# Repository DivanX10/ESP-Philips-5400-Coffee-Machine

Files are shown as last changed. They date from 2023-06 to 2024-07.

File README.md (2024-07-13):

### [Read in English here](https://github.com/DivanX10/ESP-Philips-5400-Coffee-Machine/blob/main/README_EN.md)

# ESP-Philips-5400-Coffee-Machine

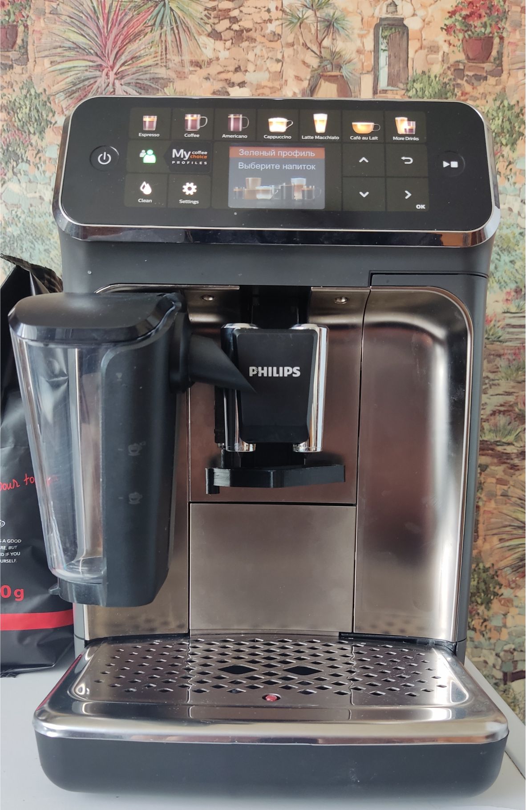
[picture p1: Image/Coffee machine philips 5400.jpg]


***

### Выражаю благодарность участникам чата [ESPHome](https://t.me/esphome) и [Умный дом с диваном](https://t.me/smart_home_divan), а также огромное спасибо [Brokly](https://github.com/Brokly) за неоценимый вклад в данный проект, который написал код для управления кофемашиной. 

***

Важно! Собирать прошивку строго в ESPHome версии 2023.5.0 или 2023.6.0 и не позднее, а также в конфигурации указывать конкретную версию arduino 2.0.9. Если соберете прошивку в последней версии ESPHome и будете использовать arduino recommended, то кофемашина будет сбоить, будет работать некорректно. Нужно переписывать код. Если имеете желание переписать код под новую версию ESPHome и поделитесь, то буду вам благодарен за участие. Спасибо. 

```
esp32:
  board: esp32dev
  framework:
    type: arduino
    version: 2.0.9
```
<details>
  <summary>Как установить любую версию аддона ESPHome?</summary>

1) Скачать нужную версию аддона ESPHome можно по этой [ссылке](https://github.com/esphome/home-assistant-addon)
 * Скачать аддон ESPHome 2023.5.0 (17.05.2023) [здесь](https://github.com/esphome/home-assistant-addon/releases/tag/2023.5.0)
 * Скачать аддон ESPHome 2023.6.0 (22.06.2023) [здесь](https://github.com/esphome/home-assistant-addon/releases/tag/2023.6.0)
2) Распаковать архив в любое место чтобы можно было скопировать в Home Assistant
3) Копируем папку **esphome** из архива в сетевую папку **addons**. Если сетевые папки Home Assistant не работают, то установить аддон **Samba share**. Аддон **Samba share** по умолчанию доступен в магазине аддонов, но если аддона **Samba share** по каким-то причинам нет, то включите расширенный режим и тогда в магазине аддонов вы увидите аддон **Samba share**, а если этого аддона по прежнему нет, то можете установить аддон **Samba share** по этой [ссылке](https://github.com/home-assistant/addons/tree/master/samba)

 * Как включить Расширенный режим?   


 * Куда скачать файл **esphome**?

В архиве **home-assistant-addon-xx.xx.xxxx** нас интересует папка **esphome**


Папку **esphome** копируем в сетевую папку **addons**



4) Перезагружаем Home Assistant
5) Заходим в магазин аддонов и ищем локальную версию аддона ESPHome. Смотрим на версию, должна быть версия 2023.5.0 или 2023.6.0, в зависимости какой архив мы скачали


8) Если локальная версия аддона ESPHome есть и версия 2023.5.0 или 2023.6.0, то ставим

</details>

***

Модификация и удаленное управление кофемашиной Philips 5400. Управление реализовано средствами UART и ESPHome.

> Важно!
Все материалы этого проекта (прошивки, схемы, 3D модели и т.п.) предоставляются "КАК ЕСТЬ". Всё, что вы делаете с вашим оборудованием, вы делаете на свой страх и риск. Автор не несет ответственности за результат и ничего не гарантирует. Модификация кофемашины требует вмешательства, что лишит автоматически вас гарантии на новую кофемашину.

> Рабочие варианты кода для управления кофемашиной можно взять [**здесь**](https://github.com/DivanX10/ESP-Philips-5400-Coffee-Machine/tree/main/Config/ESPHome) (читайте комментарии в коде)

***

<details>
  <summary>Что умеет делать интеграция?</summary>

1) Включать и выключать кофемашину
2) Выбрать кофейный напиток
   * Эспрессо
   * Эспрессо лунго
   * Кофе
   * Американо
   * Капучино
   * Латте макиато
   * Кофе с молоком
   * Кофе латте
   * Кафе крема
   * Ристретто
   * Кофе в дорогу
   * Кофе с молоком в дорогу
   * Молочная пена
   * Горячая вода
3) Выбрать крепость кофе
4) Выбрать зерно или молотый
5) Выбрать количество порции, в том числе и ExtraShot
6) Выбрать объем кофе
7) Выбрать объем молока
8) Отправлять собственные рецепты кофейных напитков
9) Автоматическая работа отвода воды от носика кофемашины
10) Калибровка сервопривода для отвода воды
11) Сенсоры
    * Поддон
    * Зерно
    * Вода в контейнере
    * Контейнер кофейной гущи
    * Поддон и контейнер воды извлечены
    * Статус питания кофемашины (включена/выключена)
    * Статусы кофемашины (приготовление, наливаем кофе, наливаем молоко, перемалываем зерна и т.д)
    * Сенсор ошибки
    * Сенсор 90 для отображения пакета рецепта кофейных напитков, этот пакет можете использовать для создания своего любимого рецепта кофейного напитка
    * Сенсор выбранного кофейного напитка, обема кофе и молока

</details>

<details>
  <summary>Добавление компонета Philips 5400 в ESPHome</summary>
  
```
external_components:
  - source:
      type: git
      url: https://github.com/DivanX10/ESP-Philips-5400-Coffee-Machine

```

При желании можно подключить компонент локально. Скачайте файлы в папку \esphome\components\ 

```
external_components:
  - source:
      type: local
      path: components
    components: [philips_series_5400]

```

</details>

<details>
  <summary>Примеры отправки собственных кофейных напитков</summary>

> Это чисто рекомендация и уведомление. Решение принимать вам. У данной модели любые изменения параметра напитка сохраняются в профиль, кроме гостевого профиля. Чтобы не перезаписывать профили, можете выбрать гостевой профиль и посылая рецепты на приготовление, изменения не будут перезаписаны. Когда отправляете любой напиток, на экране не будет отображаться выбранный вами напиток, а будет отображаться тот напиток, который вы выбирали последний раз на панели управления кофемашины. Если не трогали экран, то по умолчанию будет выбираться первый напиток, это эспрессо   

Если включить сенсор Messge2 90, то в нем будет отображаться пакет кофейного напитка. Вы можете это использовать для своих рецептов. Просто скопируйте все байты, кроме первых трех (пример на скриншоте, выделено красным)



Вы можете создавать любые рецепты используя таблицу [**протокола кофейных напитков**](https://github.com/DivanX10/ESP-Philips-5400-Coffee-Machine/raw/main/Protocol/Протокол%20кофейных%20напитков%20и%20программы.xlsx) в Excel

```
button:

#Пример кода для отправки кофейного напитка Кофе Max 150ml. Пакет рецепта копируется с сенсора Messge2 90, отсеиваем только первые 3 байта
#Напиток: Кофе. Зерно: Максимум. Кофе: 150 мл.
  - platform: template
    name: "Кофе Max 150ml"
    icon: mdi:coffee
    on_press:
      - lambda: |-
          {
            uint8_t data[]={0x00, 0x03, 0x00, 0x02, 0x02, 0x00, 0x96, 0x00, 0x00, 0x00};
            id(philip)->prepare(data);
          }

#Пример кода для отправки кофейного напитка Американо молотый 90ml. Пакет рецепта копируется с сенсора Messge2 90, отсеиваем только первые 3 байта
  - platform: template
    name: "Американо молотый 80ml"
    icon: mdi:coffee
    on_press:
      - lambda: |-
          {
            uint8_t data[]={0x01, 0x00, 0x00, 0x02, 0x03, 0x00, 0x28, 0x00, 0x28, 0x00};
            id(philip)->prepare(data);
          }

#Пример кода для отправки кофейного напитка Кофе с молоком 150/120ml. Пакет рецепта копируется с сенсора Messge2 90, отсеиваем только первые 3 байта
  - platform: template
    name: "Кофе с молоком Max 150/120ml"
    icon: mdi:coffee
    on_press:
      - lambda: |-
          {
            uint8_t data[]={0x02, 0x03, 0x00, 0x02, 0x01, 0x02, 0x96, 0x00, 0x78, 0x00};
            id(philip)->prepare(data);
          }

```
</details>

<details>
  <summary>Встраиваем ESP</summary>

Снимаем панель управления. Снимается не сложно. Чуть тянем на себя, в эти точки вставляем пластиковую лопатку и вынимаем панель



Нам нужен доступ к 8-ми жильному проводу, который нужно подключить к ESP. 





> Подключаем по схеме на выбор, через реле или через оптопару. Сервопривод подключаем по желанию, он нужен для работы отвода воды от носика.

### Общая схема подключения без реле и оптопары. Просто подключение ESP32 к кофемашине



***

### Схема с подключением реле 5В (KY-019)



***

### Cхема с подключением оптопары PC817C



</details>

<details>
  <summary>Разбираем панель управления</summary>

Почему именно я разобрал панель управления и подключил реле, и почему не оптопару? Были попытки найти решение включить кофемашину без разборки панели управления. Пробовал размыкать питание через транзистор, пробовал посылать посылать команды, но это было безуспешно. 

Подключал резистор по такой схеме, но этот способ работает на кофемашине серии 2000/3000, но не подошел для серии 5400. Для справки, есть два проекта для кофемашин серии 2000, это [ESPHome-Philips-Smart-Coffee]( https://github.com/TillFleisch/ESPHome-Philips-Smart-Coffee) и [SmartPhilips2200](https://github.com/chris7topher/SmartPhilips2200)

Снимаем наклейку с чипа и видим маркировку с названием чипа STM32L4R5VIT6




В документации чипа [STMicroelectronics STM32L4R5VIT6](https://github.com/DivanX10/ESP-Philips-5400-Coffee-Machine/blob/main/Documentation/STMicroelectronics%20STM32L4R5VIT6.pdf) находим наш чип, это STM32L4R5VIT6 LQFP100 (25 ножек с каждой стороны)



В документации пишется, что управлять кофемашиной байтами можно после включения, поэтому у меня и не получилось включить ее удаленно. Возможно я ошибаюсь и если будет найдено такое решение, то обязательно внесу поправку



***

Для имитации работы сенсорной кнопки можно использовать модуль реле одноканальный 5В (KY-019) или оптопару PC817C, которые будут подавать GND на резистор R110, к которому идет дорожка от кнопки питания, тем самым включая и выключая кофемашину. Я не стал рисковать припаивать провод после резистора R110 (номинал резистора 4,7 кОм), так как после резистора идет прямая дорожка к ножке чипа, а лампе к конденсаторам и я не знаю как чип может на это отреагировать, но, если так сделать, то тогда у нас будет возможность включать кофемашину через сенсорную кнопку и удаленно. Это было проверенно на сенсорной лампе, где я припаял провода после резистора и я мог включать и выключать удаленно, а также включать и выключать лампу нажимая на сенсорную кнопку. На кофемашине я не решаюсь это повторить.

Панель управления в разборе




Дорожка от кнопки питания к резистору R110(номинал резистора 4,7 кОм), после резистора дорожка идет к [диоду шоттки BAS70TW (K73)](https://github.com/DivanX10/ESP-Philips-5400-Coffee-Machine/blob/main/Documentation/Диод%20шоттки%20BAS70TW%20(K73).pdf)





Припаиваем провод к резистору R110(номинал резистора 4,7 кОм)



Делаем отверстие в крышке и выносим провод наружу, который подключим к реле или к оптопаре



</details>

<details>
  <summary>Расшифровка протокола</summary>

> Мне удалось расшифровать часть протоколов, если вы найдете что-то новое, сообщите мне об этом обновлю информацию. Создайте ишью и опишите подробно про протокол. 

Краткое описание функции протоколов

* **AA:AA:AA:90** - рецепты кофейных напитков
* **AA:AA:AA:91** - счетчик приготовления кофейных напитков
* **AA:AA:AA:93** - счетчик приготовления кофейных напитков
* **AA:AA:AA:B0** - системные сенсоры
* **AA:AA:AA:B5** - счетчик объема кофе и молока для приготовления кофейных напитков
* **AA:AA:AA:BA** - не смог расшифровать
* **AA:AA:AA:BB** - не смог расшифровать
* **AA:AA:AA:FF** - данные с ЖК экрана
* **AA:AA:AA:FE** - включение и выключение кофемашины

***

**AA:AA:AA:FE** - этот пакет AA:AA:AA:FE:00:00:C8:87:1B:40:55 встречается два раза, в самом начале, он идет первым, когда включаем кофемашину и при выключении

**AA:AA:AA:90** - протокол кофейных напитков




**AA:AA:AA:91** - протокол счетчика кофейных напитков. Это просто учет сделанных кофейных напитков и учет сбрасывается, когда кофемашина выключается. Сделали одну чашку кофе, сработал счетчик и выставил допустим 1, потом сделали еще чашку кофе, снова сработал счетчик и выставил 2. Чтобы удаленно запускать приготовление кофейных напимтков, нужно запускать на +1 к тому, что в счетчике. Без учета этого счетчика не будет срабатывать приготовление кофейных напитков удаленно



**AA:AA:AA:B0** - протокол системных сенсоров: контейнер кофейной гущи, воды, поддона, анличие зерна, статусы приготовления кофе, статусы заварного блока



**AA:AA:AA:B5** - протокол счетчика кофейных напитков. Считает в секундах объем налитого кофе и молока



</details>

<details>
  <summary>Отвод воды носика кофемашины</summary>

Я разработал для кофемашины отвод воды от носика. Зачем это нужно? Когда включаем кофемашину, то при включении запускается прогрев и промывка. Во время промывки большая часть воды проходит внутри, а часть выливается через носик. Что делать, если мы хотим, чтобы утром кофемашина приготовила нам свежее кофе и чтобы в кофе не было воды после промывки? Отвод воды позволяет решить эту проблему. Когда кофемашина включается с помощью умного дома, то отовод воды все еще остается у носика вполть до того момента, когда кофемашина не передейдет в режим "Выбор напитка", только после этого отвод воды прячется во внутрь носика, открывая проход носику.

Готовую модель для распечатки на 3д принтере можете [здесь](https://www.thingiverse.com/thing:6073849) или [скачать с этого проекта](https://github.com/DivanX10/ESP-Philips-5400-Coffee-Machine/tree/main/3D%20Model). Файлы формата FCStd можете открыть в программе FreeCAD. 

Используется сервопривод MG90S Micro Servo 180 градусов. Его вполне достаточно для отвода воды. Питаем от +3,3в от самого ESP, что является большим плюсом. Провод от сервопривода во внутрь протягивается просто, без сверления корпуса. Протискиваем провод во внутрь держателя носика и тянем к внутренней части корпуса к ESP




</details>

<details>
  <summary>Панель управления в Home Assistant</summary>





Скопируйте код [отсюда](https://github.com/DivanX10/ESP-Philips-5400-Coffee-Machine/blob/main/Config/Home%20Assistant/coffee_machine_philips_5400_ru.yaml), а после создайте карточку

Код карточки
```
entity: sensor.coffee_machine_power_status
type: custom:multiple-entity-row
name: Статус
icon: mdi:coffee-maker
state_color: true
show_state: false
secondary_info:
  attribute: Making coffee
entities:
  - entity: group.kitchen_coffee_machine_info_and_menu
    name: Меню
    state_color: true
    icon: mdi:information-outline
    styles:
      height: 60px
      width: 50px
  - entity: group.kitchen_coffee_machine_coffee_drinks
    name: Напитки
    state_color: true
    icon: mdi:coffee
    styles:
      height: 60px
      width: 50px
  - entity: switch.coffee_philips_5400_valve_open_closed
    name: Клапан
    type: switch
    tap_action:
      action: toggle
    icon: mdi:coffee-maker-outline
    state_color: true
    styles:
      height: 60px
      width: 50px
  - entity: binary_sensor.coffee_philips_5400_power_status
    name: Питание
    icon: mdi:gesture-tap-button
    state_color: true
    tap_action:
      action: call-service
      service: script.kitchen_coffee_machine_power
    styles:
      height: 60px
      width: 50px

```
</details>

</details>

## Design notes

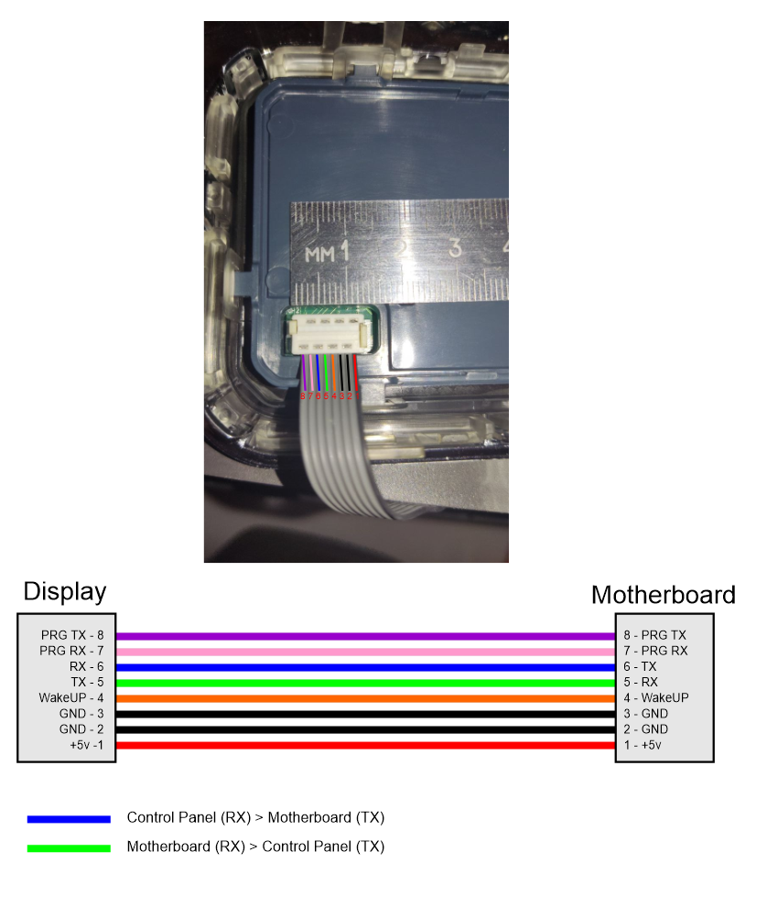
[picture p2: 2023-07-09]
Image/Pinout of 8-core wire en.png

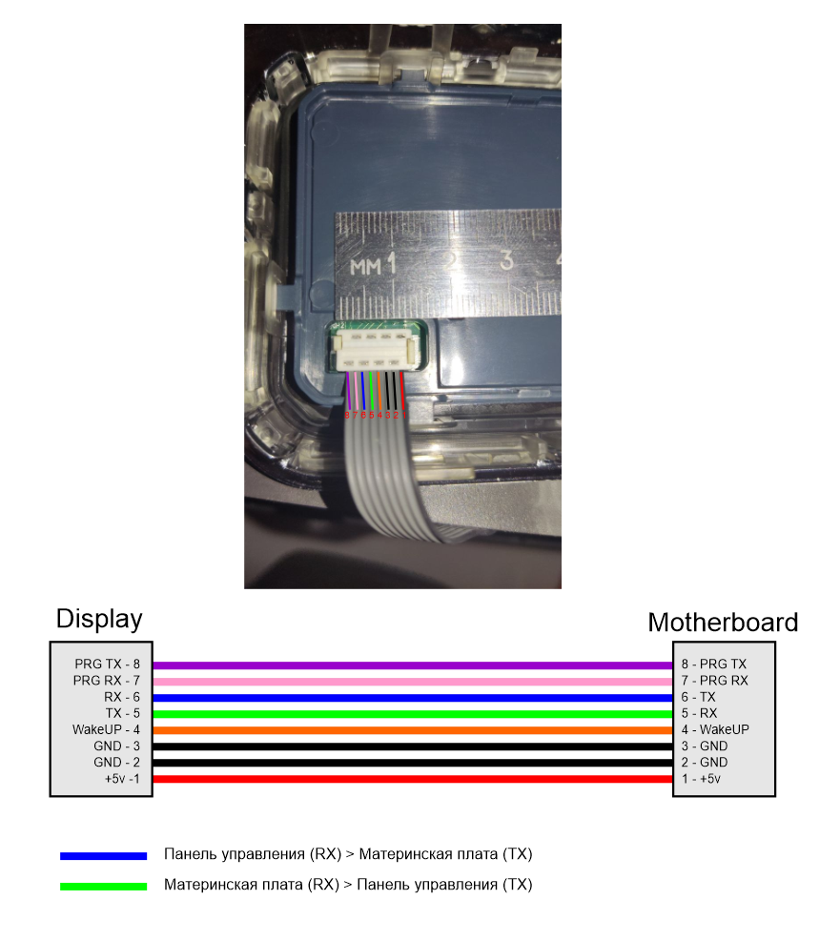
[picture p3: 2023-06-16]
Image/Pinout of 8-core wire.png

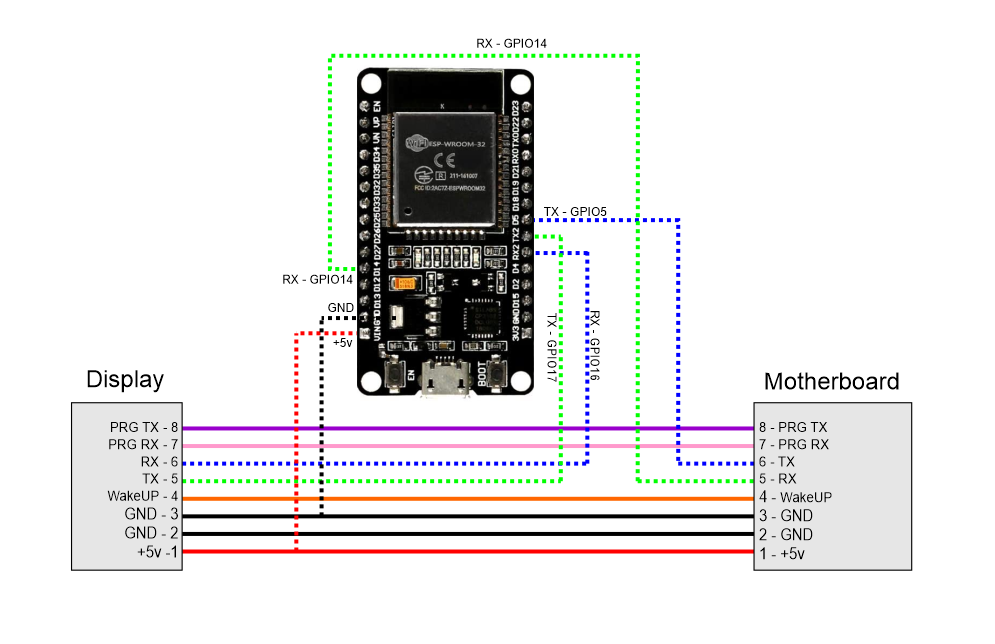
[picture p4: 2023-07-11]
Image/ESP connection diagram.png

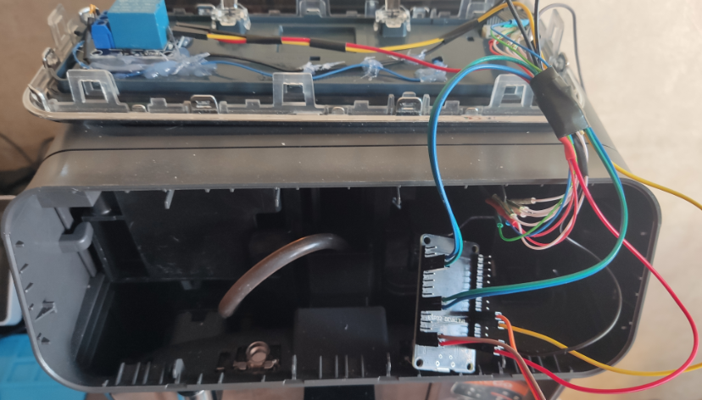
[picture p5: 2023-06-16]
Image/Connecting ESP.png

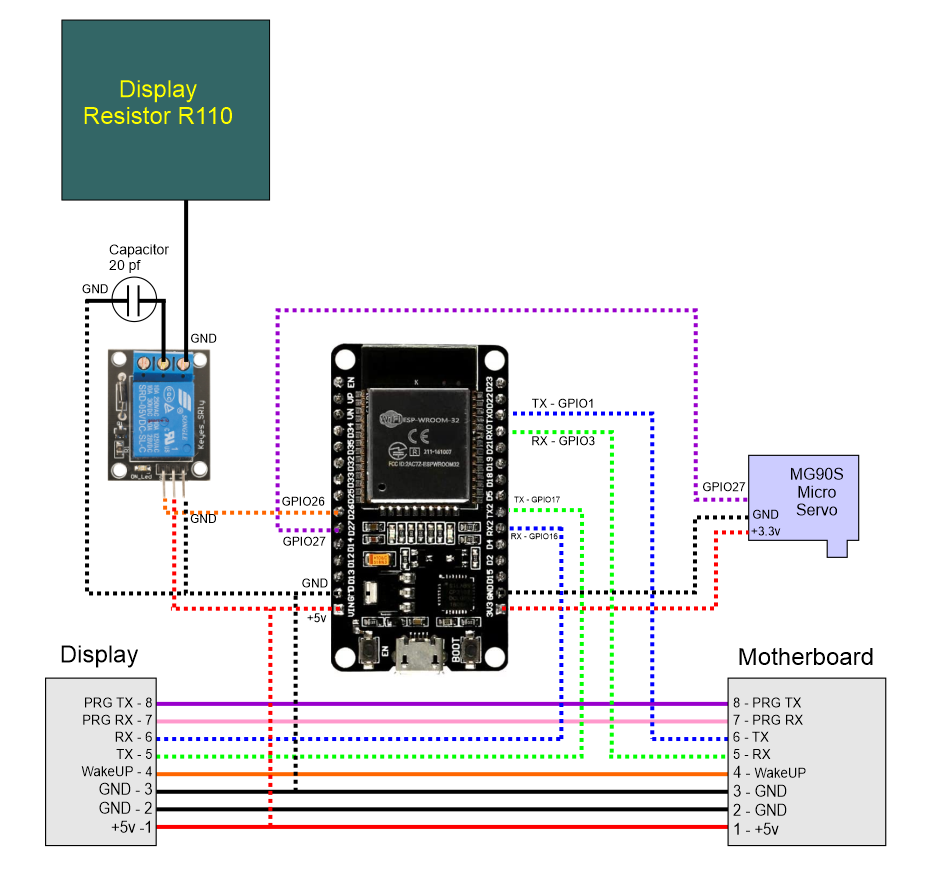
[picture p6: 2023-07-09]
Image/ESP + KY-019 relay + servo connection diagram.png

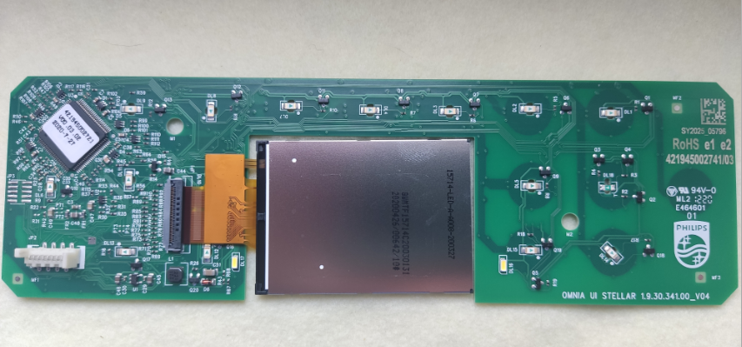
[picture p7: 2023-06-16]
Image/Chamber from the control panel.png

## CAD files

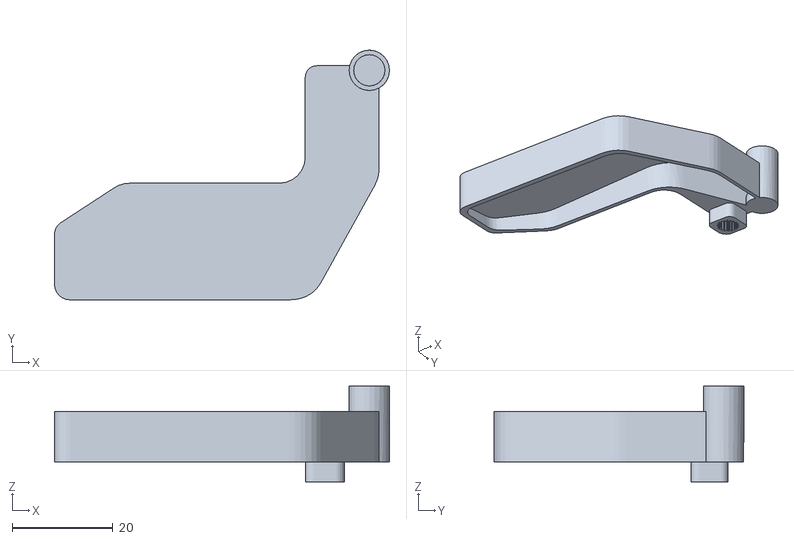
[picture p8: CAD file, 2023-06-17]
3D Model/Drainage of water from the spout.stl
66.4 x 49.5 x 19.0

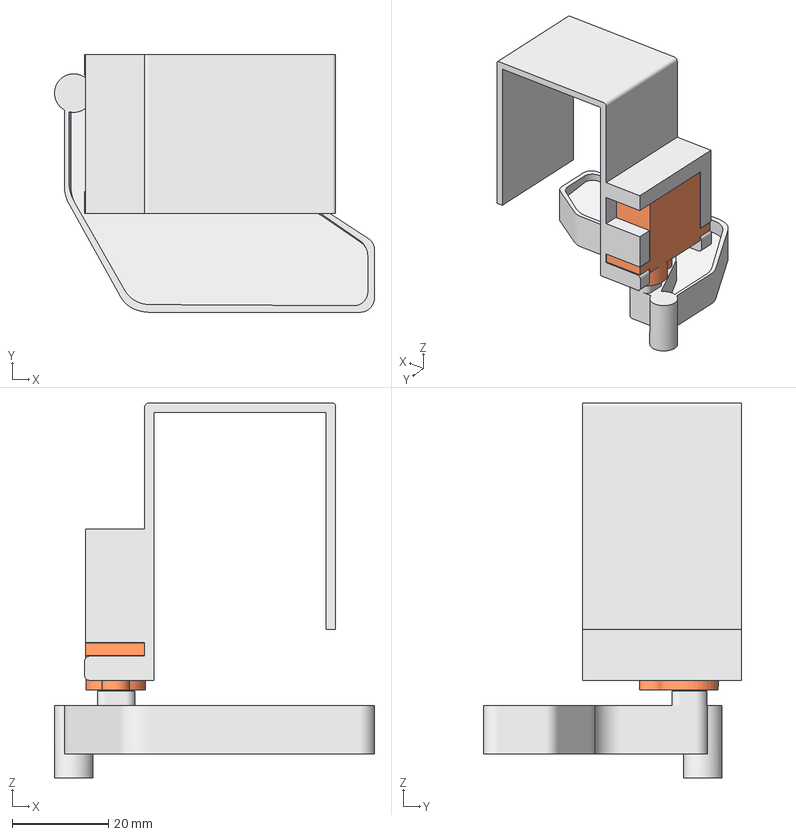
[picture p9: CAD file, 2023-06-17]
3D Model/Serva holder on the spout bracket.FCStd
66.4 x 53.5 x 77.8 mm
Держатель сервы002
Отвод воды с носика (Вариант 2)
MG90S Micro Servo

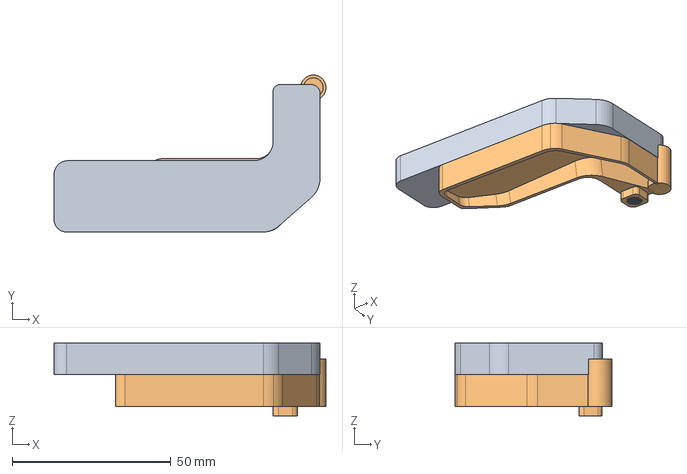
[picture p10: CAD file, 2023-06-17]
3D Model/Water drain of the coffee machine spout.FCStd
85.7 x 49.5 x 23.0 mm
Отвод воды с носика006

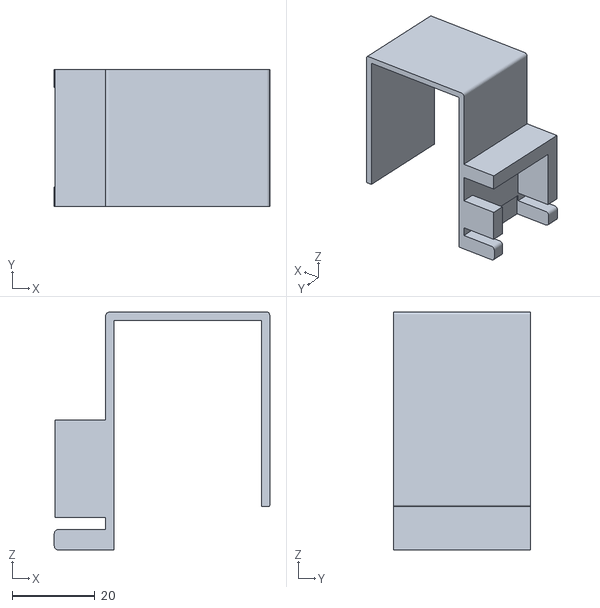
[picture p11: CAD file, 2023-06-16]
3D Model/Serva holder.stl
52.1 x 33.0 x 57.5

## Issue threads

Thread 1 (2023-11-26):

Power up without cleaning cycle

Sandst4, 2023-11-26:
First of all, amazing what you have accomplished! Really nice to be able to connect the 5400 to home assistant.

I've came across this project through here:

https://github.com/TillFleisch/ESPHome-Philips-Smart-Coffee

Inside that project they have been able to turn on the Philips Series 2200 without it starting the cleaning cycle. They accomplish this by sending a specific command. Do you think this could be possible for the 5400 as well?

I love your 3D printed solution, however, being able to skip the cleaning cycle and only do it when turning off would be amazing. Thanks!

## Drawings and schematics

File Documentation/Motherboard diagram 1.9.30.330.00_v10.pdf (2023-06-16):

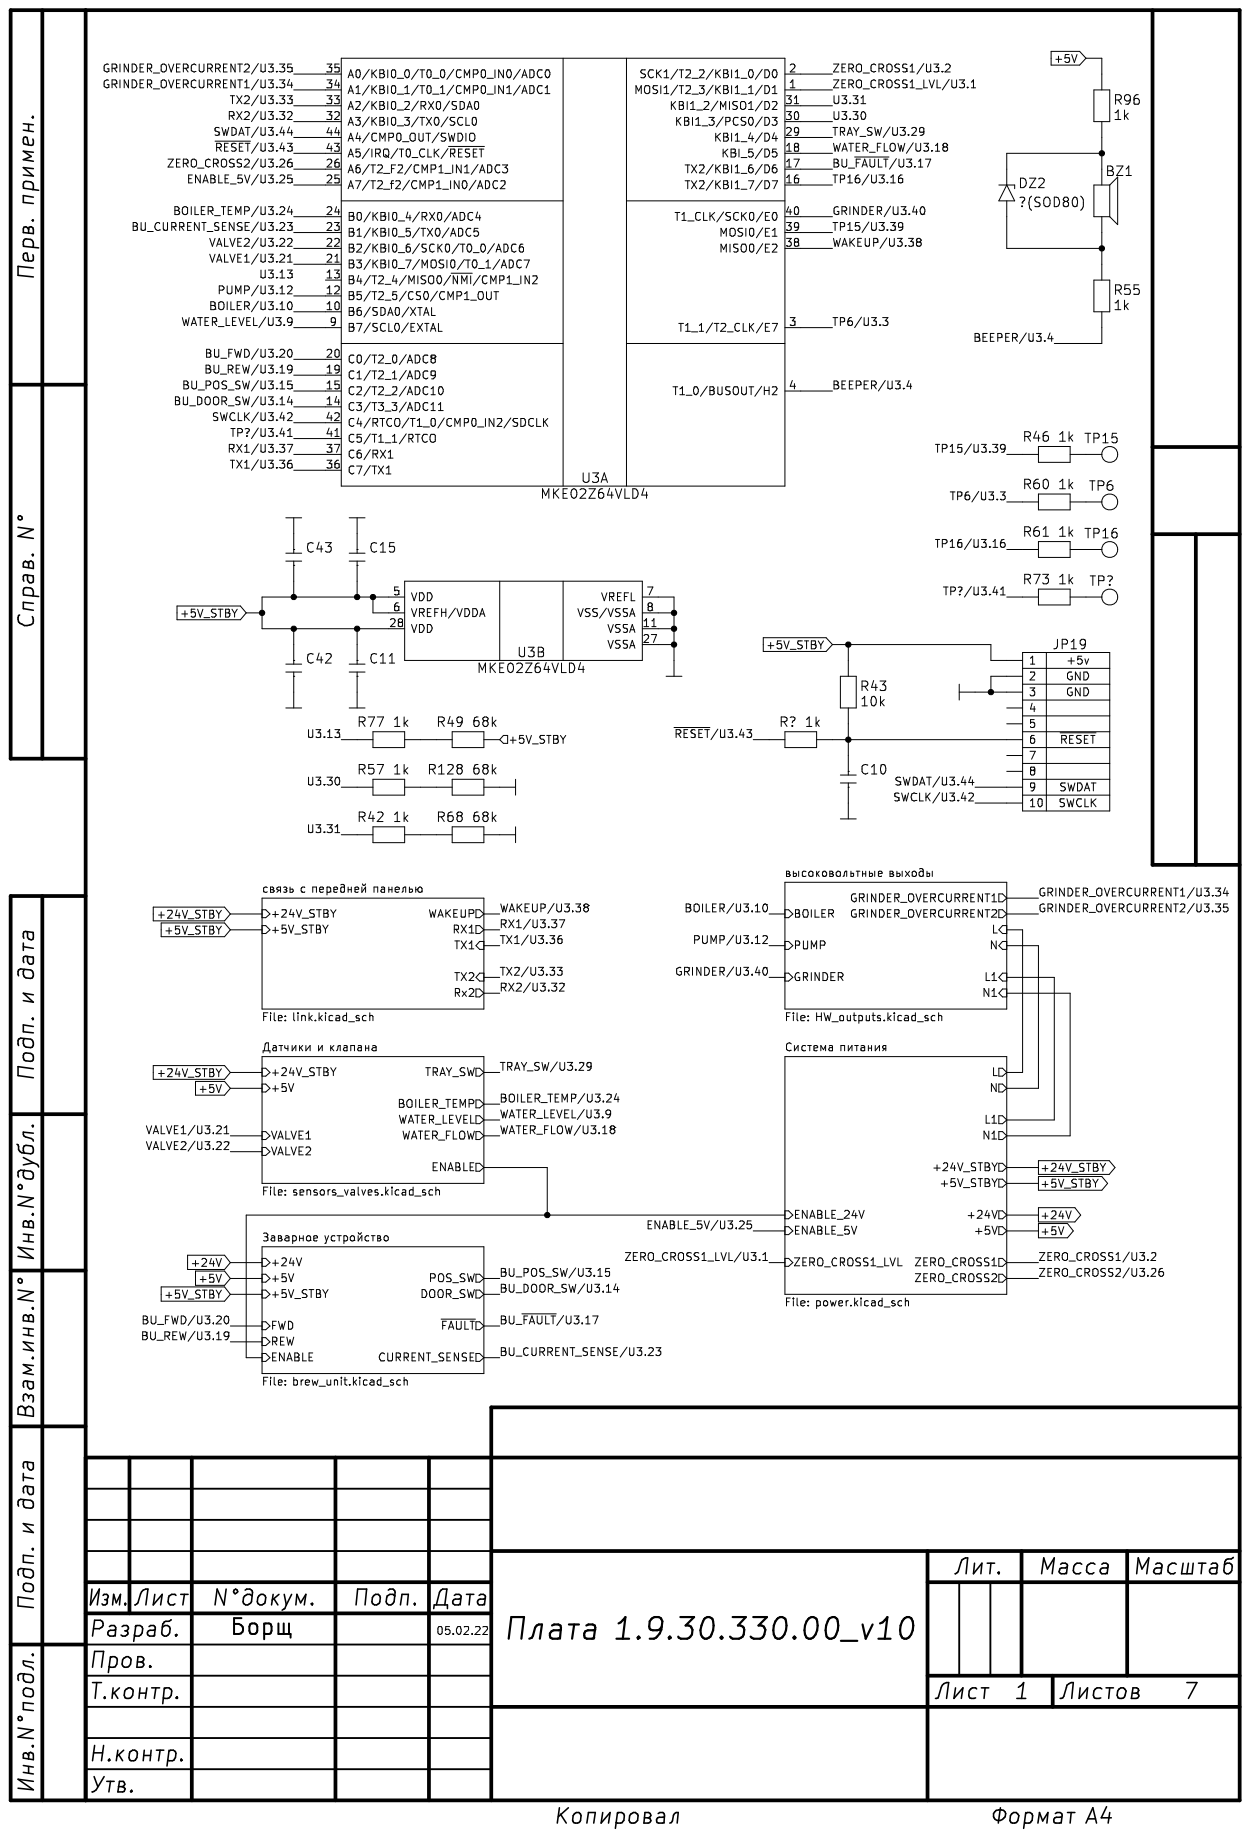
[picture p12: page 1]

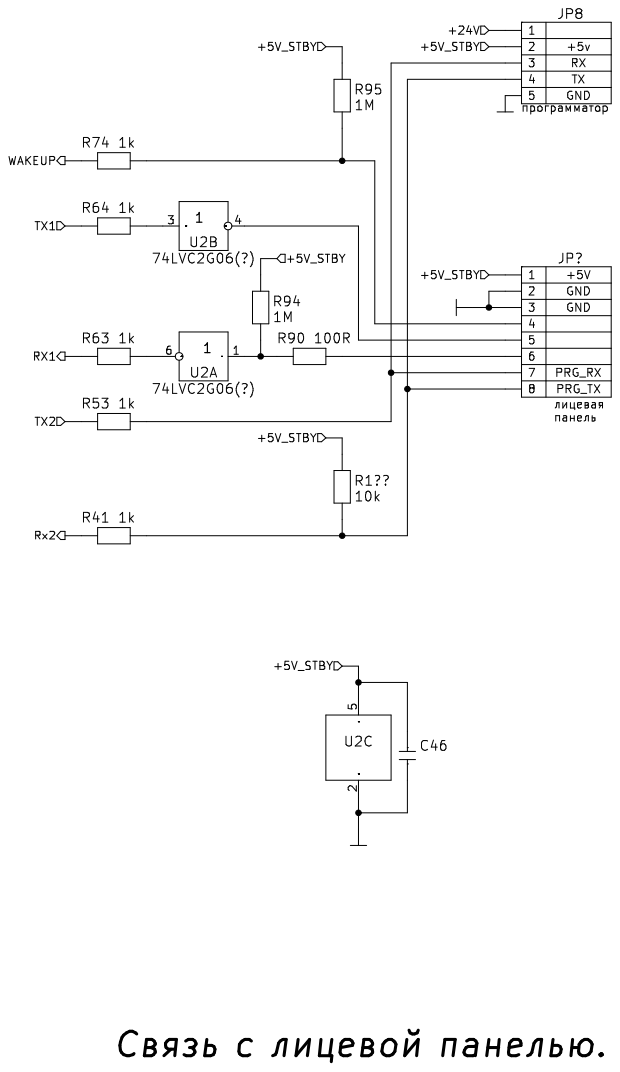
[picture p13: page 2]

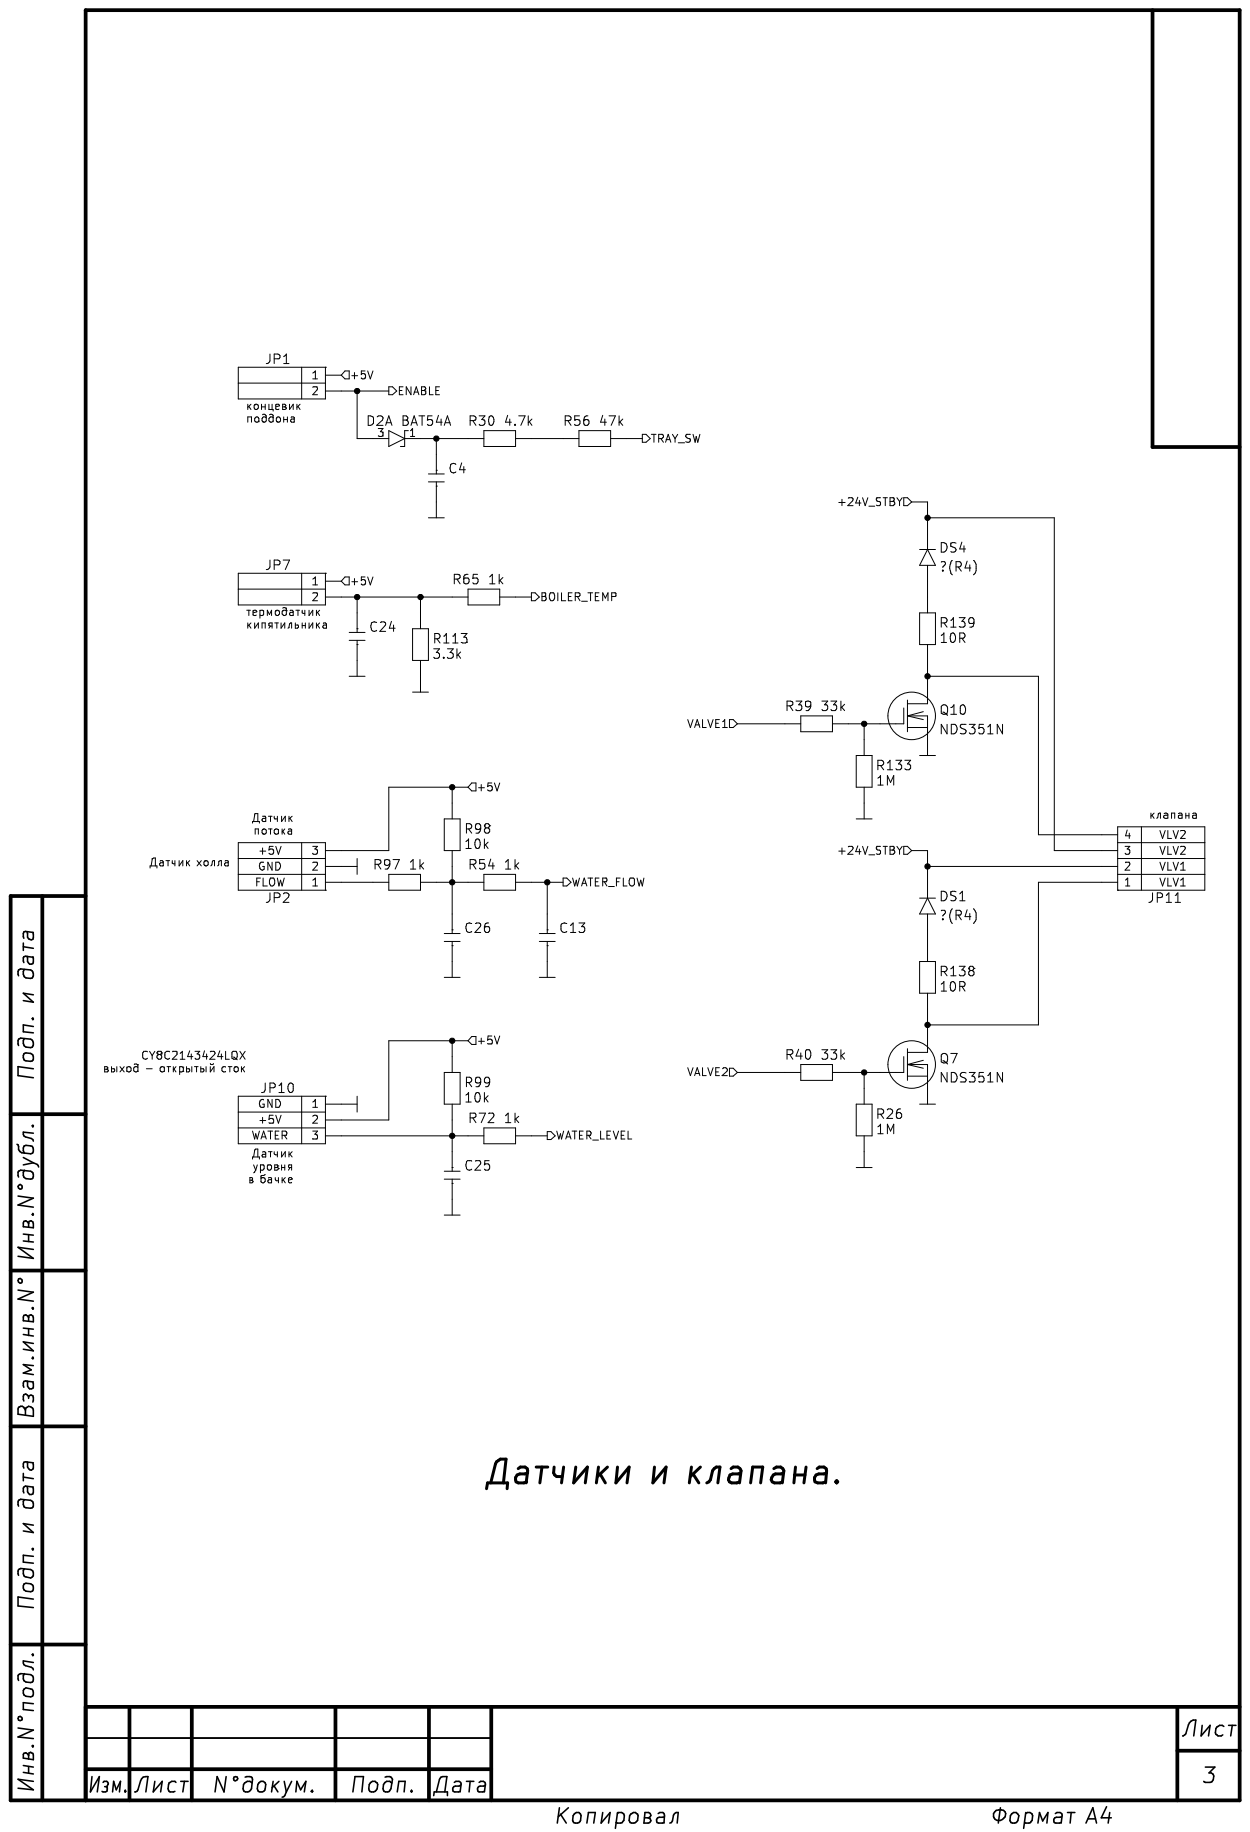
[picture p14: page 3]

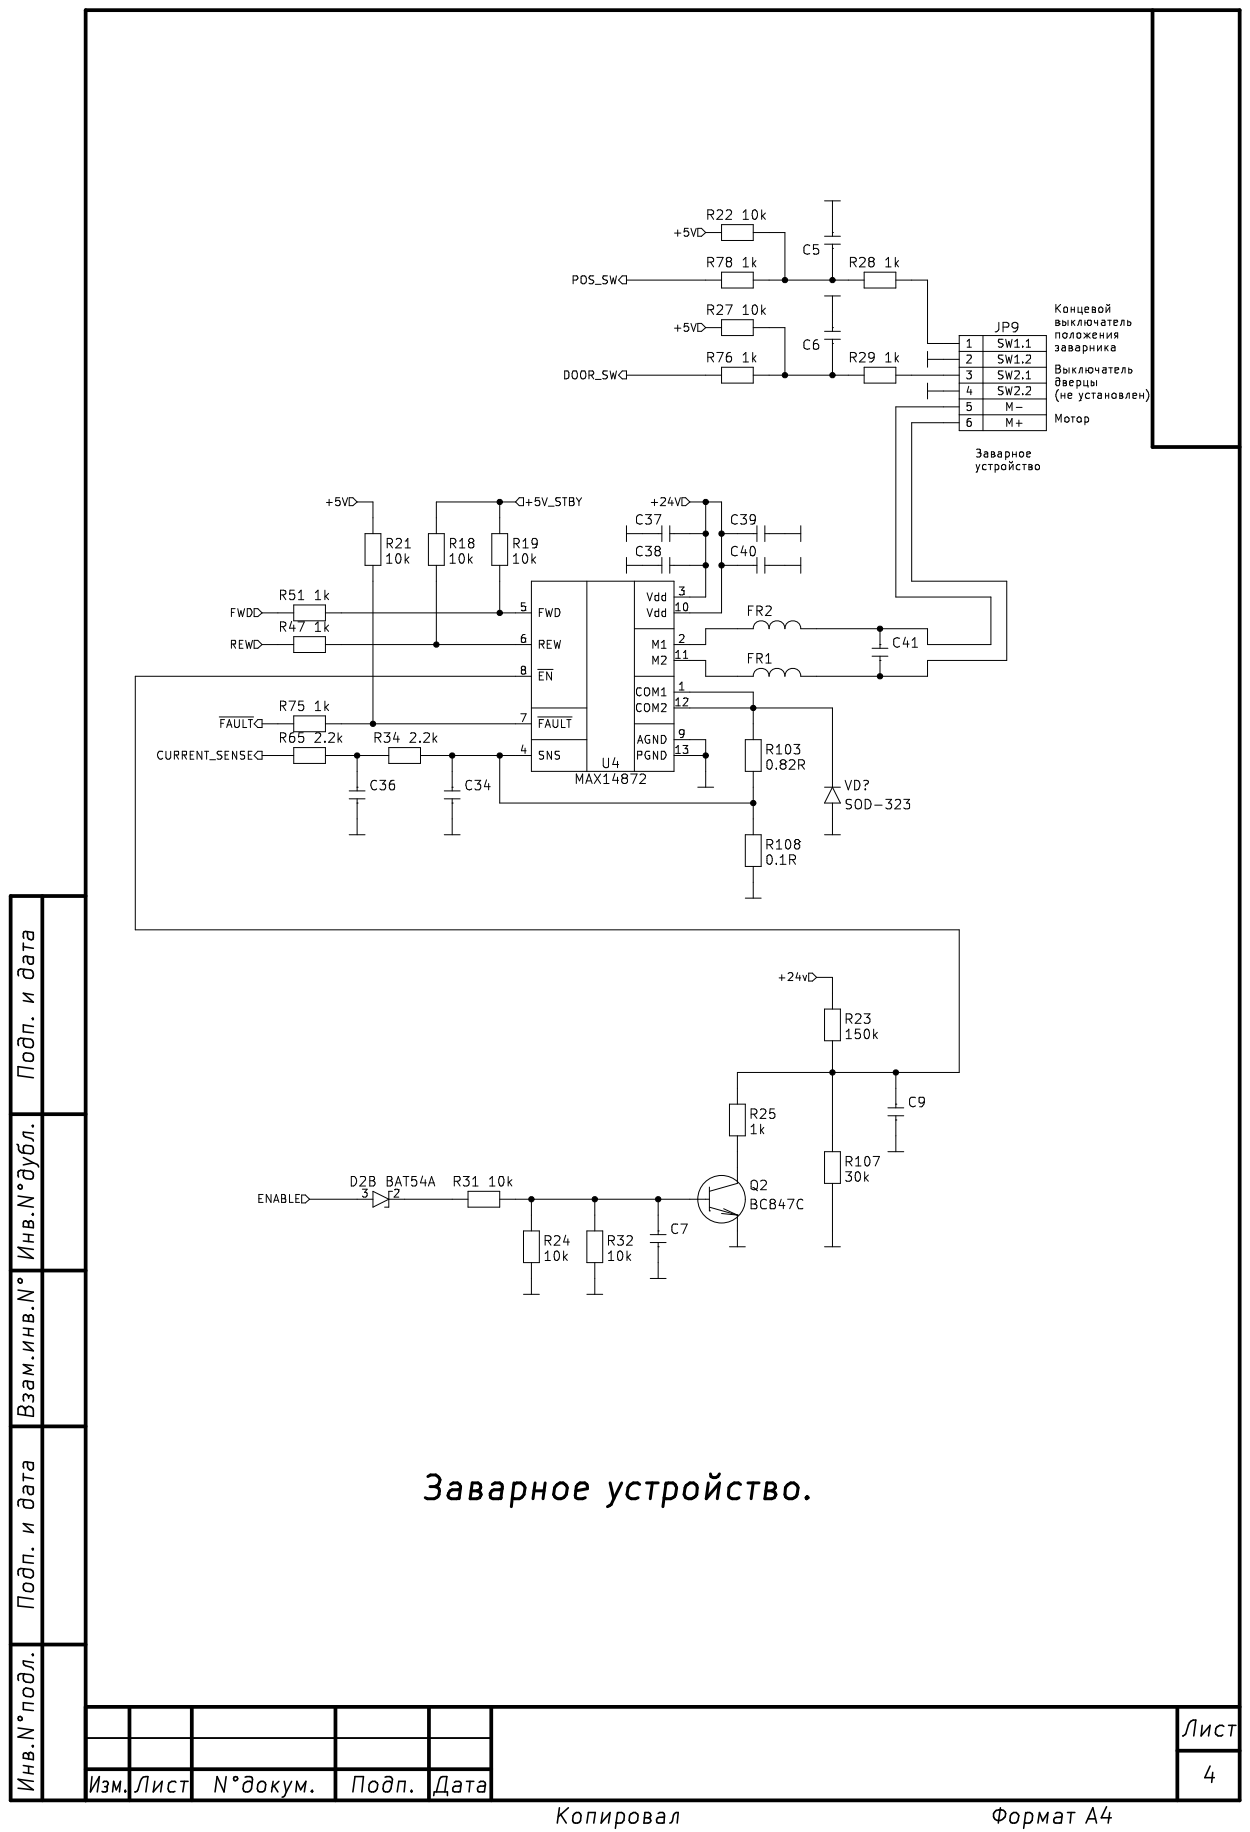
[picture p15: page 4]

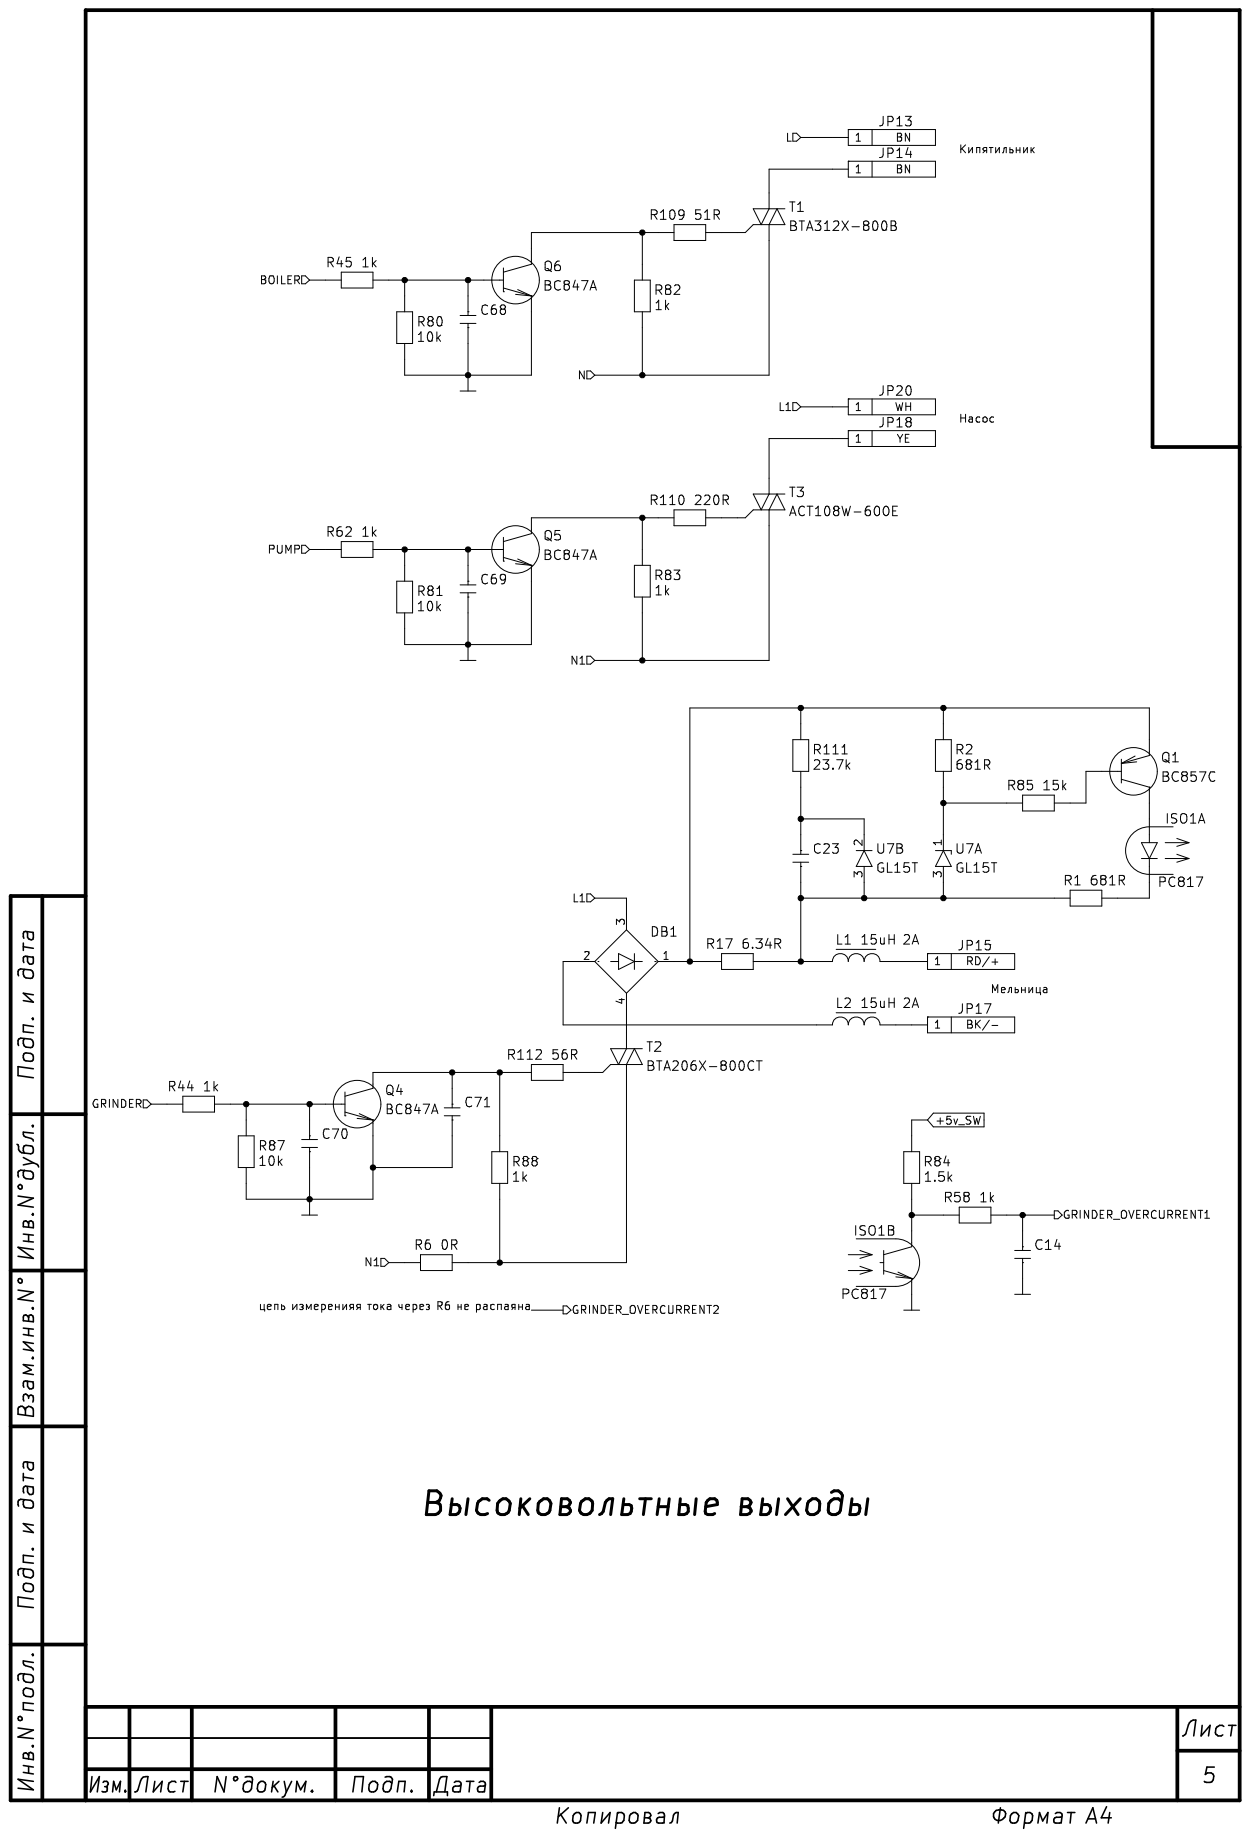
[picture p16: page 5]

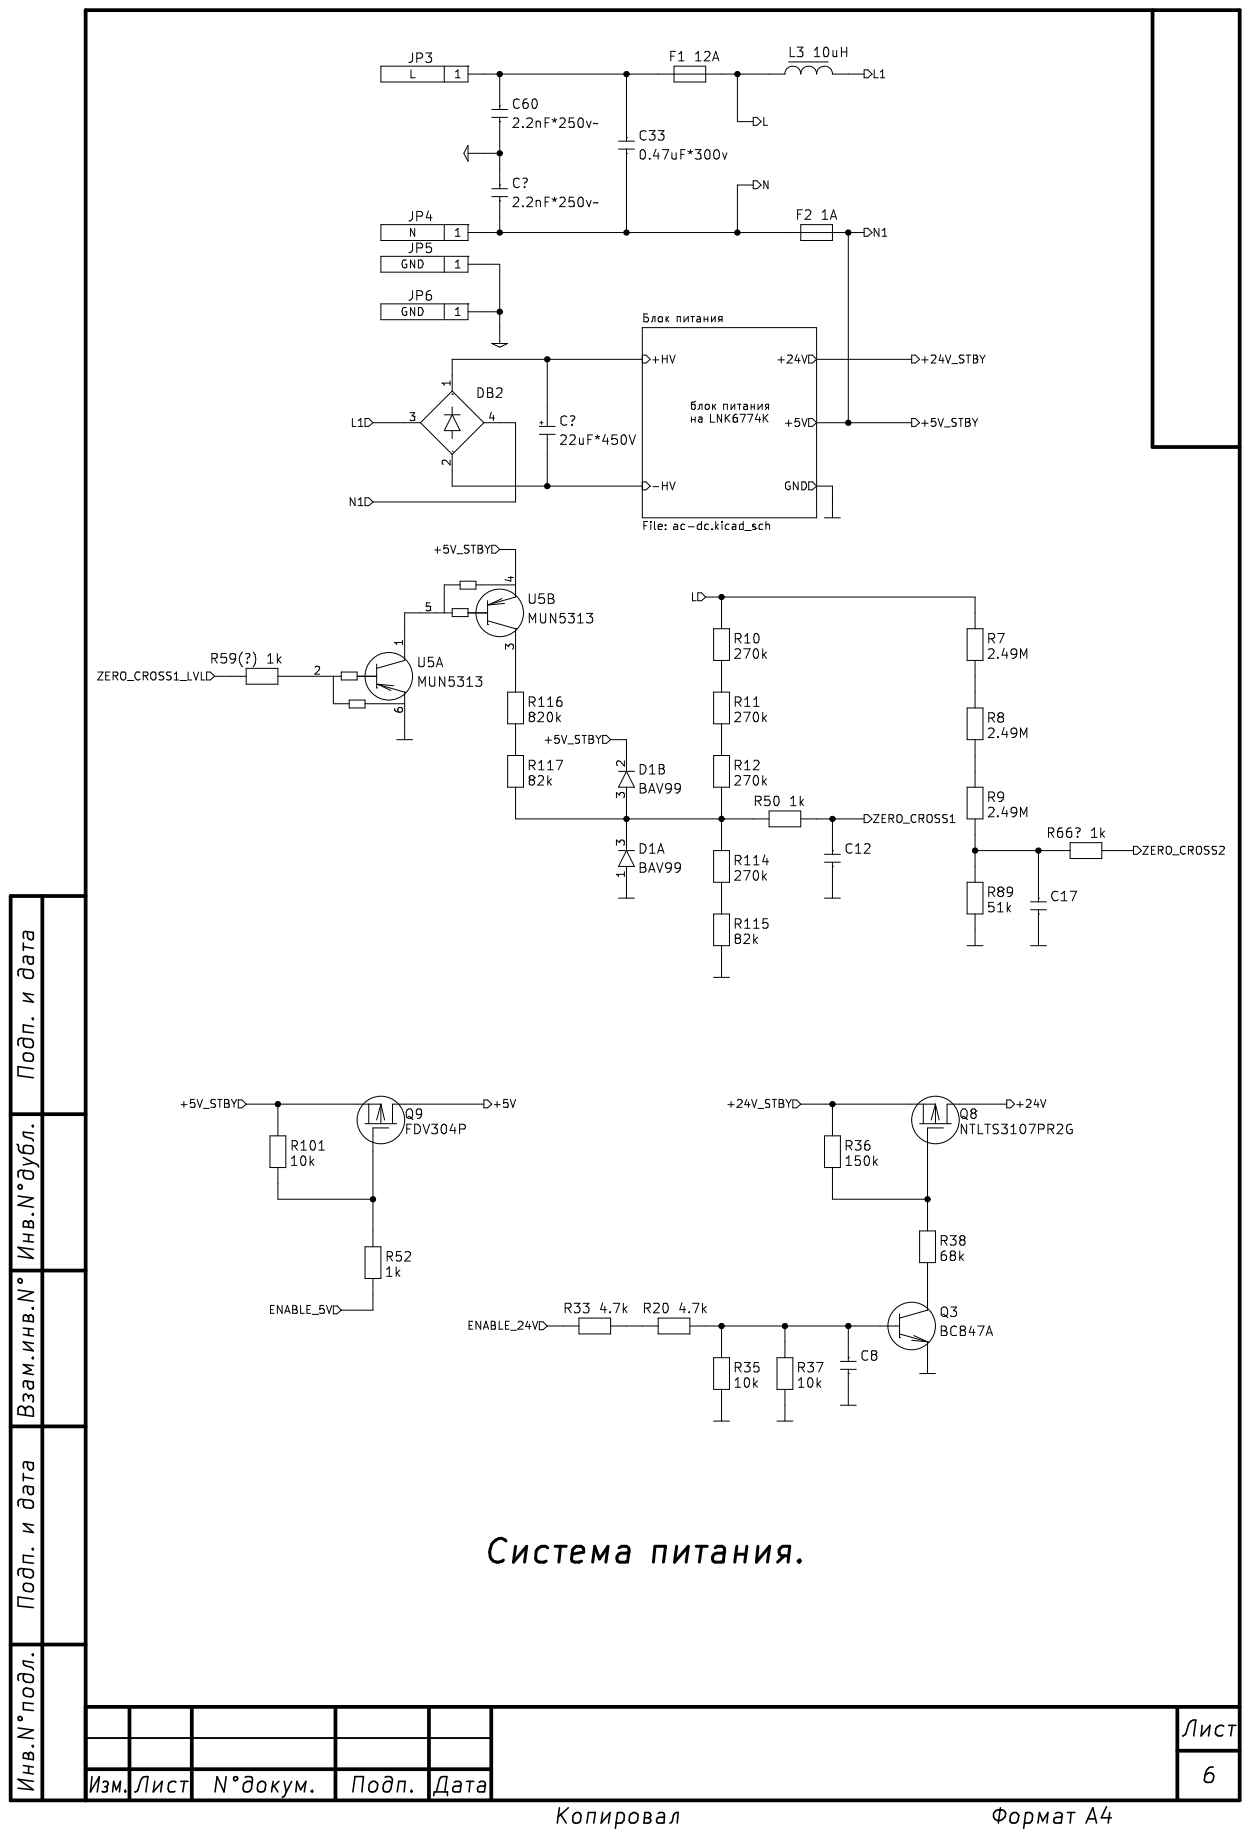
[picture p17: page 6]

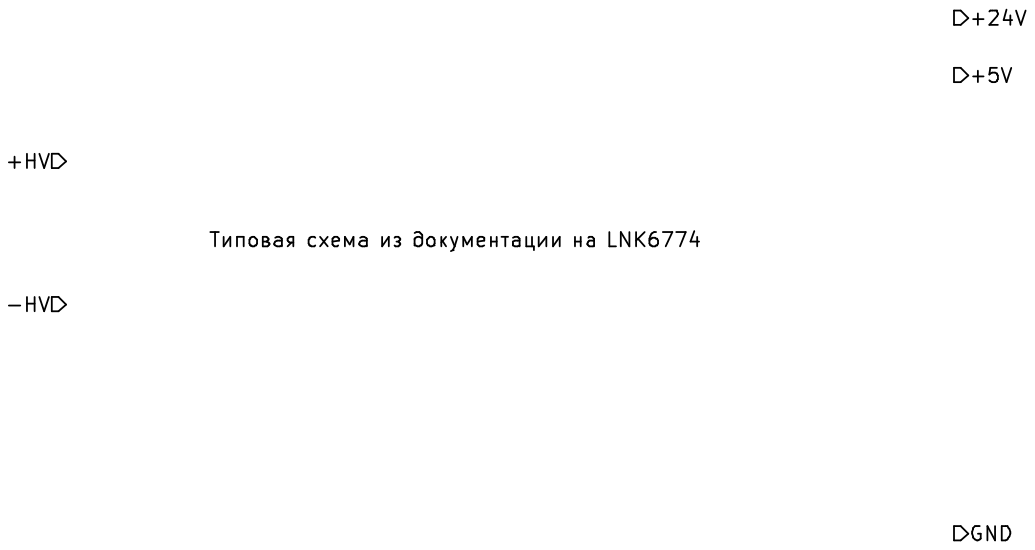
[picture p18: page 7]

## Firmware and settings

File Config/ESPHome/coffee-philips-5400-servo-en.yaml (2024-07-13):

#This option is equipped with a servo drive and automatic water removal from the spout of the coffee machine
#Connect the MG90S Micro Servo
#Added a servo for the water pump of the coffee machine spout
#Added a switch for automatic operation of water drainage
#Added some examples of a coffee drink to understand where and how to add your favorite coffee drinks

substitutions:
  board_name: Coffee Philips 5400
  node_name: coffee-philips-5400

esphome:
  name: ${node_name}
  friendly_name: coffee-philips-5400
  comment: ESP32 Coffee Philips 5400

esp32:
  board: esp32dev
  framework:
    type: arduino
    version: 2.0.9 #Strictly collect in ESPHome version 2023.5.0 or 2023.6.0

#Wi-Fi credentials for connecting the board to the home network
wifi:
  ssid: !secret wifi_ssid
  password: !secret wifi_password
  fast_connect: off
  reboot_timeout: 15min

#If there is no connection with WiFi, then the access point will rise
  ap:
    ssid: ESP SmartCoffeePhilips
    password: !secret ap_esp_password

#The captive portal component in ESPHome is a backup mechanism in case of a connection failure to the configured Wi-Fi
captive_portal:

#The web server is turned off on purpose, since the coffee machine turns off spontaneously at any moment
#web_server:
#  port: 80

#Logging
logger:
  level: ERROR #NONE
  baud_rate: 0

#Enable OTA
ota:
  password: "esphome"

#Enable Home Assistant API
#Encryption turned off to reduce the load on the ESP
api:


#####################################################################################
############################## Output Platform #####################################
output:
  - platform: ledc
    id: pwm_output
    pin: GPIO27
    frequency: 50 Hz

#####################################################################################
################################ Configuration #######################################
#MG90S Micro Servo Servo
servo:
  - id: idServoControl
    output: pwm_output
    auto_detach_time: 5s #Idle time, after which the servo is automatically disconnected
    transition_length: 2s #The time it takes for the servo to move smoothly between different positions
    restore: true #Restoring the servo position after a reboot or power failure
    min_level: 5% #The minimum level of the PWM signal. Pulse = 1 ms, hence min_level = 1 * 100 / 20 = 5%
    idle_level: 7.5% #The average level of the PWM signal. Pulse = 1.5 ms, hence idle_level = 1,5 * 100 / 20 = 7.5%
    max_level: 10% #The maximum level of the PWM signal. Pulse = 2 ms, hence max_level = 2 * 100 / 20 = 10%


#####################################################################################
################################## External component ################################
external_components:
  - source:
      type: git
      url: https://github.com/DivanX10/ESP-Philips-5400-Coffee-Machine

#####################################################################################
######################################### UART ######################################
uart:
 - id: uart_display
   rx_pin: GPIO16
   tx_pin: GPIO17
   baud_rate: 115200
   stop_bits: 1
   data_bits: 8
   parity: NONE
   rx_buffer_size: 256

 - id: uart_mainboard
   rx_pin: GPIO14
   tx_pin: GPIO5
   baud_rate: 115200
   stop_bits: 1
   data_bits: 8
   parity: NONE
   rx_buffer_size: 256


######################################################################################
################################## Connected component ##############################
philips_series_5400:
  display_uart: uart_display
  mainboard_uart: uart_mainboard
  restore_value: true
  debug: true #Debugging mode. If enabled, then when choosing a drink, coffee volume, milk, portion, a recipe package will be displayed
  id: philip 
  #Sensors for publishing messages in text form. In order for the sensor to be displayed, comment
  #B0_msg:
  #  name: Messge B0 #System sensors
  #B5_msg:
  #  name: Messge B5 #Coffee and milk volume counter for making coffee drinks
  #BA_msg:
  #  name: Messge BA #Couldn't decipher it
  90_msg: 
    name: Messge2 90 #Coffee Drink Recipes
  #91_msg:
  #  name: Messge3 91 #Coffee Beverage Preparation Counter
  #93_msg:
  #  name: Messge1 93 #Coffee Beverage Preparation Counter
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

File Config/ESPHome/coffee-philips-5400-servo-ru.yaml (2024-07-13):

#Этот вариант с сервоприводом и автоматическим отводом воды от носика кофемашины
#Подключаем сервопривод MG90S Micro Servo
#Добавлен сервопривод для овтода воды носика кофемашины
#Добавлен выключатель автоматической работы отвода воды
#Добавлены несколько примеров кофейного напитка, чтобы понимать куда и как добавлять свои любимые кофейные напитки


substitutions:
  board_name: Coffee Philips 5400
  node_name: coffee-philips-5400

esphome:
  name: ${node_name}
  friendly_name: coffee-philips-5400
  comment: ESP32 Coffee Philips 5400

esp32:
  board: esp32dev
  framework:
    type: arduino
    version: 2.0.9 #Строго собирать в ESPHome версии 2023.5.0 или 2023.6.0

#Учетные данные Wi-Fi для подключения платы к домашней сети
wifi:
  ssid: !secret wifi_ssid
  password: !secret wifi_password
  fast_connect: off
  reboot_timeout: 15min

#Если не будет связи с WiFi, то поднимется точка доступа
  ap:
    ssid: ESP SmartCoffeePhilips
    password: !secret ap_esp_password

#Компонент captive portal в ESPHome является резервным механизмом на случай сбоя подключения к настроенному Wi-Fi
captive_portal:

#Веб сервер выключен специально, так как кофемашина выключается самопроизвольно в любой момент
#web_server:
#  port: 80

#Журналирование
logger:
  level: ERROR #NONE
  baud_rate: 0

#Обновление по воздуху (OTA)
ota:
  password: "esphome"

#Enable Home Assistant API
#Шифрование выключил для снижения нагрузки на ESP
api:


#####################################################################################
############################## Платформа вывода #####################################
output:
  - platform: ledc
    id: pwm_output
    pin: GPIO27
    frequency: 50 Hz

#####################################################################################
################################ Конфигурация #######################################
#Сервопривод MG90S Micro Servo
servo:
  - id: idServoControl
    output: pwm_output
    auto_detach_time: 5s #Время бездействия, после которого сервопривод автоматически отсоединяется
    transition_length: 2s #Время, которое требуется для плавного перемещения сервопривода между различными позициями
    restore: true #Восстановление положения сервопривода после перезагрузки или сбоя питания
    min_level: 5% #Минимальный уровень ШИМ-сигнала. Импульс = 1 ms, следовательно min_level = 1 * 100 / 20 = 5%
    idle_level: 7.5% #Средний уровень ШИМ-сигнала. Импульс = 1,5 ms, следовательно idle_level = 1,5 * 100 / 20 = 7,5%
    max_level: 10% #Максимальный уровень ШИМ-сигнала. Импульс = 2 ms, следовательно max_level = 2 * 100 / 20 = 10%


#####################################################################################
################################## Внешний компонент ################################
external_components:
  - source:
      type: git
      url: https://github.com/DivanX10/ESP-Philips-5400-Coffee-Machine

#####################################################################################
######################################### UART ######################################
uart:
#UART подключение к панели управления. Считываем данные которые приходят от материнской плате в панель управления
 - id: uart_display
   rx_pin: GPIO16 #Считываем данные с панели управления
   tx_pin: GPIO17 #Посылаем данные в панель управления
   baud_rate: 115200
   stop_bits: 1
   data_bits: 8
   parity: NONE
   rx_buffer_size: 256

 - id: uart_mainboard
   rx_pin: GPIO14 #Считываем данные с материнской платы
   tx_pin: GPIO5 #Посылаем данные в материнскую плату
   baud_rate: 115200
   stop_bits: 1
   data_bits: 8
   parity: NONE
   rx_buffer_size: 256


#####################################################################################
################################ Подключенный компонент #############################
philips_series_5400:
  display_uart: uart_display
  mainboard_uart: uart_mainboard
  restore_value: true
  debug: true #Режим отладки. Если включить, то при выборе напитка, объема кофе, молока, порции, будет отображаться пакет рецептов
  id: philip 
  #Cенсоры публикации сообщений в текстовом виде. Чтобы сенсор отображался, расскоментируйте
  #B0_msg:
  #  name: Messge B0 #Системные сенсоры
  #B5_msg:
  #  name: Messge B5 #Счетчик объема кофе и молока для приготовления кофейных напитков
  #BA_msg:
  #  name: Messge BA #Не смог расшифровать
  90_msg: 
    name: Messge2 90 #Рецепты кофейных напитков
  #91_msg:
  #  name: Messge3 91 #Счетчик приготовления кофейных напитков
  #93_msg:
  #  name: Messge1 93 #Счетчик приготовления кофейных напитков
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

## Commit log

2023-07-09 Update Кофейные напитки пакеты данных.txt
2024-07-10 Update coffee-philips-5400-en.yaml
    esp32:
    board: esp32dev
    framework:
    type: arduino
    version: 2.0.15
2024-07-10 Update coffee-philips-5400-ru.yaml
    ota:
    - platform: esphome
    password: "esphome"
    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
2024-07-10 Update coffee-philips-5400-servo-en.yaml
    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
    [coffee-philips-5400-servo-en.yaml]
2024-07-10 Update coffee-philips-5400-servo-ru.yaml
    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
    [coffee-philips-5400-servo-ru.yaml]
